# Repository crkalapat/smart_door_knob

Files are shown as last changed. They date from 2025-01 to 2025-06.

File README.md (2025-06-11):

# Smart Door Knob

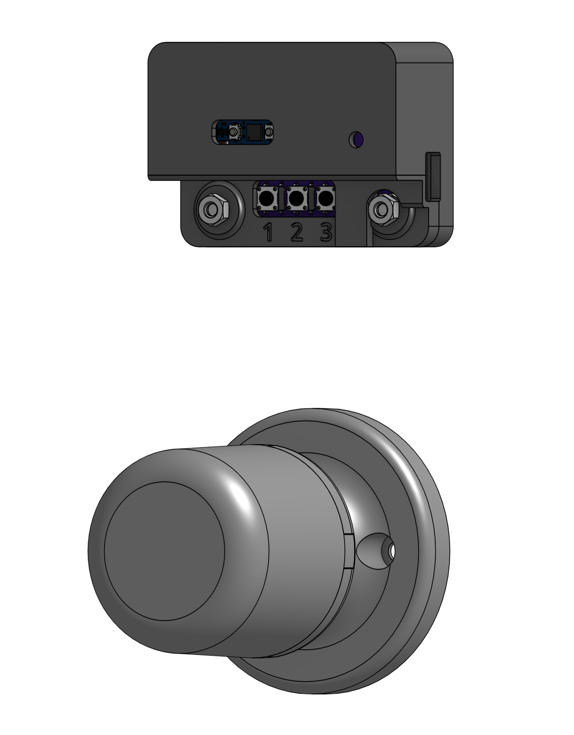
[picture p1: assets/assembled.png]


*A Matter compatible smart door knob*

## Overview
This smart door knob is designed specifically for Kwikset bed/room door knobs. The door knob is compatible with the [Matter](https://en.wikipedia.org/wiki/Matter_(standard)) smart home protocol, so it works with Amazon Alexa, Apple HomeKit, and Google Home. The only requirement is that you have a [Thread Border Router](https://www.matteralpha.com/explainer/thread-border-router) for the microcontroller (Arduino Nano Matter) to connect to.

## Instructions
After the code is flashed, you will need to set it up. You can use the QR Code link provided in the terminal, or use a manual pairing code. Once paired, (and whenever it turns on/resets after that) the RGB LED will begin to pulse blue. This signifies that it is in the process of connecting to the Thread Border Router that you specificed.

Once connected, the LED will turn off, indicating that the process has finished and that the door lock is ready to be controlled. You can then freely control the door lock either through your Matter smart home, or manually with the buttons. When the door is locked, the LED will be red, and when unlocked, the LED will be green. To unlock the door manually, enter the passcode specified in the code under the `buffer` variable (1-1-3-2 by default) using the corresponding buttons 1, 2, or 3. To lock the door manually, simply press any combination of incorrect buttons, and the door will lock if it wasn't locked already.

If you hit a wrong button and want to clear your input, simply wait for 5 seconds and all button input will be erased. If this is too long, the `inputWaitTime` variable can be customized in the code to change the clear time.

## Firmware Installation
Open the repo folder in Arduino IDE. If needed, pin numbers for components such as the RGB LED, servo, and buttons can be changed manually in the Arduino code file. Flash the code onto the Arduino Nano Matter. Once done, in the Serial Monitor (115200 baud), information for pairing the door lock can be found and used with a Matter compatible device.

## BOM
- 1x [Arduino Nano Matter with headers](https://store-usa.arduino.cc/collections/internet-of-things/products/nano-matter) (or [similar board](https://github.com/SiliconLabs/arduino/blob/main/readme.md))

- 2x 1x15 Socket Headers

- 1x [MG90 Servo](https://www.amazon.com/MG90S-Servo-Motor-Helicopter-Arduino/dp/B07L6FZVT1?crid=VYZSRM9027BT) (SG90 also works)

- 3x [6mm Push Buttons](https://www.amazon.com/DAOKI-Miniature-Momentary-Tactile-Quality/dp/B01CGMP9GY?crid=3P0EFZBRL88C4&)

- 1x [Micro USB Connector](https://www.mouser.com/ProductDetail/Amphenol-FCI/10118194-0011LF?qs=9lcNTSmDlCqQOdqcAswPOg%3D%3D)

- 1x [RGB LED](https://www.amazon.com/EDGELEC-Tri-Color-Multicolor-Diffused-Resistors/dp/B077XGF3YR?crid=3S7KMO6E8I0PC)

- 1x [PCB Board](pcb/)

- 8x M3x12mm screws

- 7x [Custom 3D-printed parts](cad/printed)

- 6x M3 nuts

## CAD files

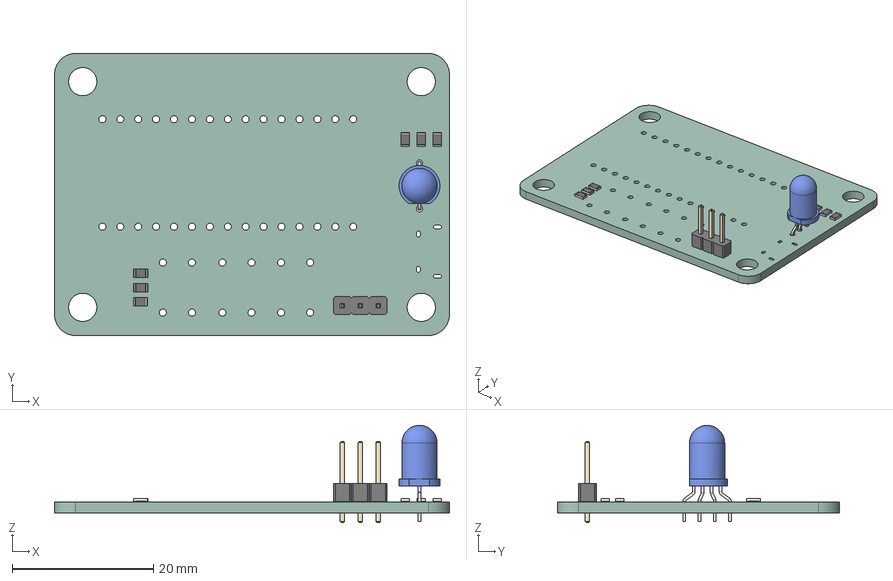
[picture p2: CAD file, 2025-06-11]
cad/pcb.step
56.0 x 40.0 x 13.8 mm
R_0805_2012Metric x 6
LED_D5.0mm-4_RGB_Wide_Pins
PinHeader_1x03_P254mm_Vertical
DoorKnob_PCB

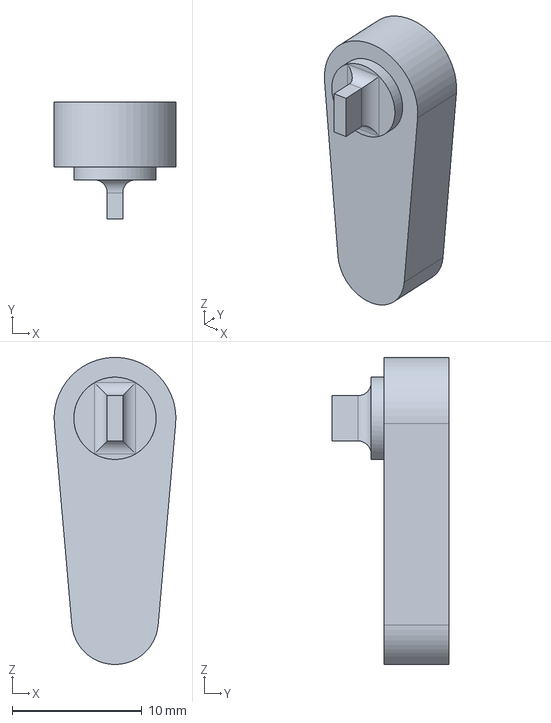
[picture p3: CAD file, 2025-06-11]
cad/printed/Servo Case.step
9.39 x 9.00 x 23.7 mm

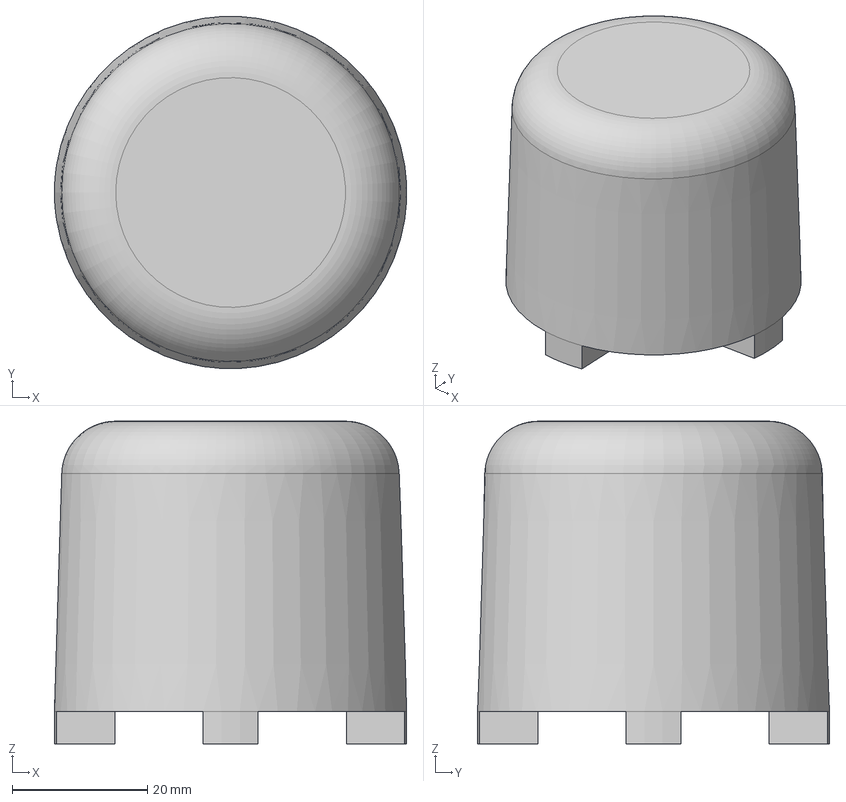
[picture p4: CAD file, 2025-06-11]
cad/printed/Knob Barrel.step
52.1 x 52.1 x 47.8 mm

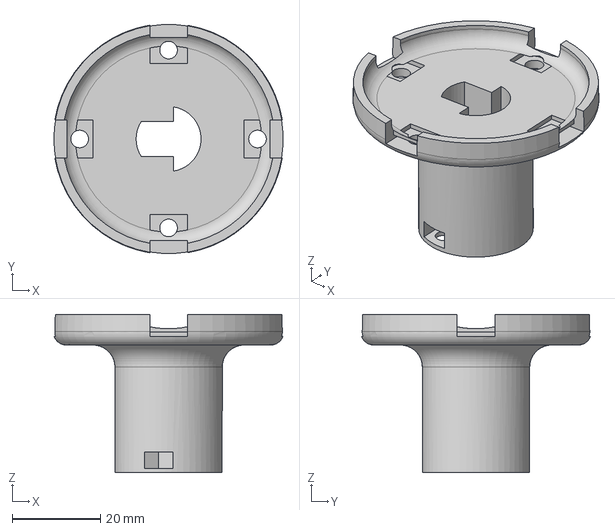
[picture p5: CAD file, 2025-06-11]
cad/printed/Knob Arm.step
52.0 x 52.0 x 36.0 mm

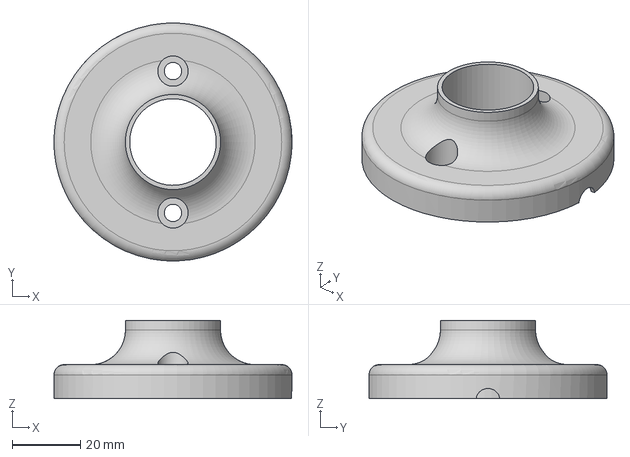
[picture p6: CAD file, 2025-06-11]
cad/printed/Knob Base.step
69.8 x 69.8 x 23.0 mm

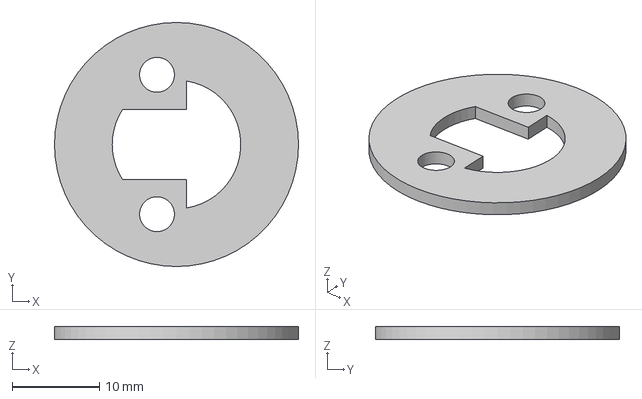
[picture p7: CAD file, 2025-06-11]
cad/printed/Knob Stopper.step
28.0 x 28.0 x 1.50 mm

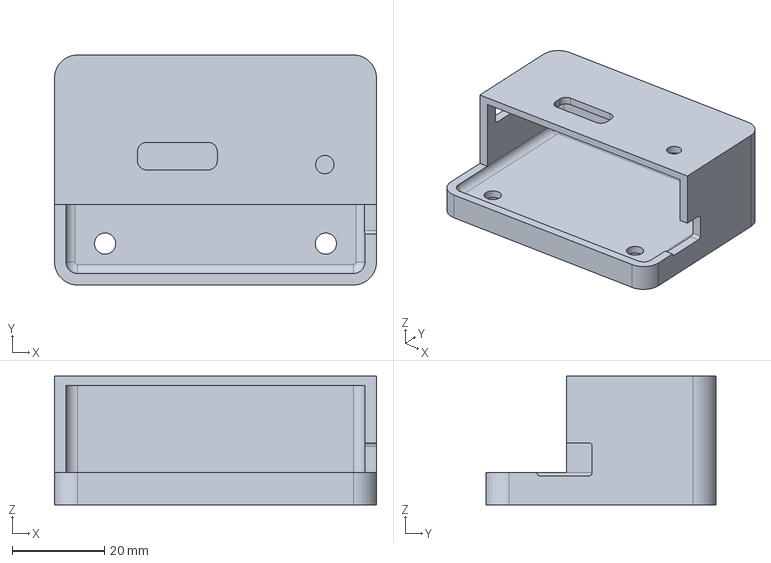
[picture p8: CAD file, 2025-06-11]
cad/printed/Electronics Enclosure.step
70.0 x 50.0 x 28.0 mm

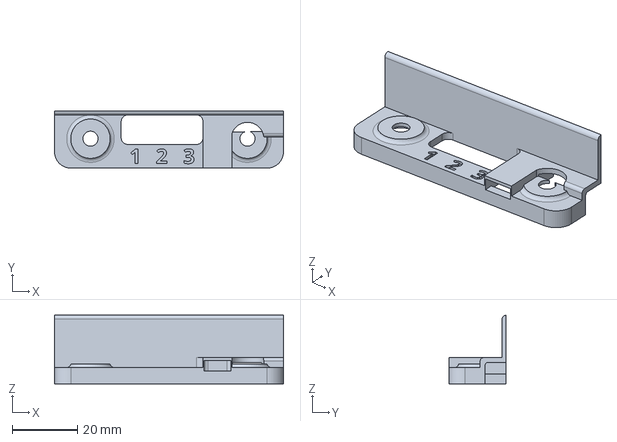
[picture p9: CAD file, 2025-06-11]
cad/printed/Electronics Lid.step
70.0 x 17.5 x 21.0 mm

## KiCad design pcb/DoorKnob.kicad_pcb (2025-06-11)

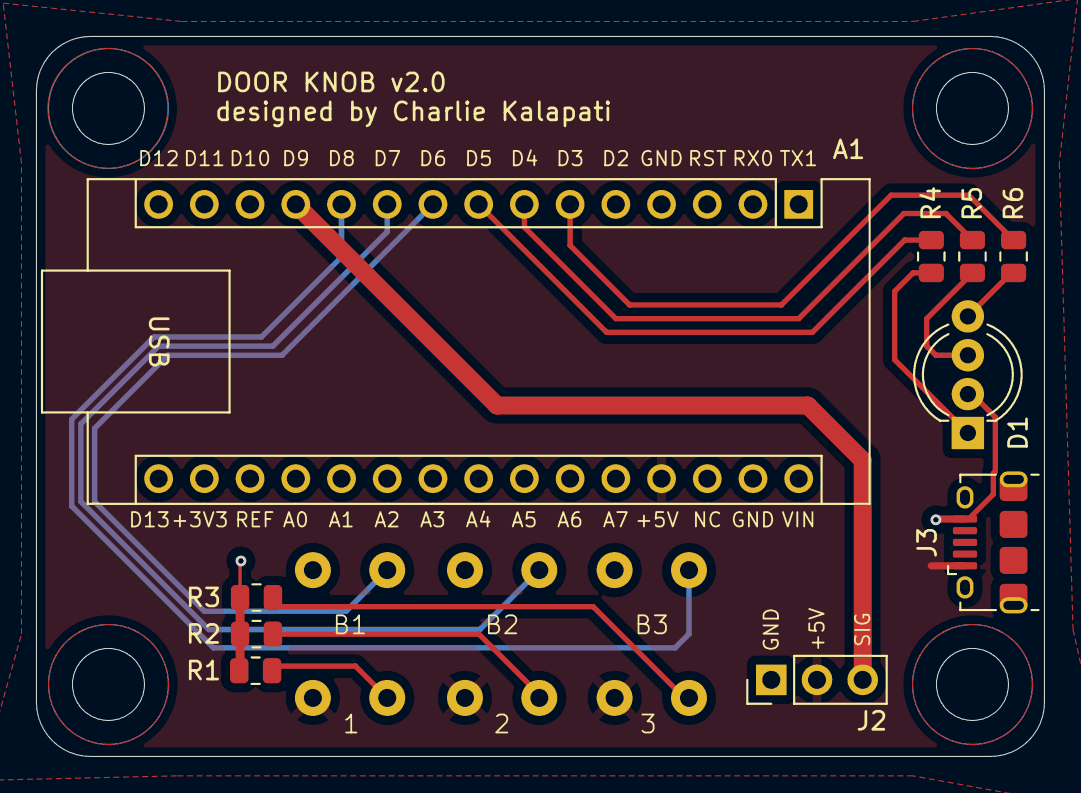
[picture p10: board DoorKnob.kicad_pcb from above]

Board: 2 copper layers, 56.0 x 40.0 mm, 13 parts (0 on the bottom side), 15 nets.

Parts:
A1: Arduino_Nano_Matter; Arduino_Nano
B1, B2, B3: Button_6mm
D1: LED_RKGB; LED_D5.0mm-4_RGB_Wide_Pins
J2: Conn_01x03; PinHeader_1x03_P2.54mm_Vertical
J3: USB_B_Micro; USB_Micro-B_Amphenol_10118194-0001LF_Horizontal
R1, R2, R3, R4, R5, R6: 220R; R_0805_2012Metric

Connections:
+5V: A1.27 (+5V), B1.3, B2.3, B3.3, J2.2, J3.1 (VBUS)
GND: A1.29 (GND), D1.2 (K), J2.1, J3.5 (GND), R1.2, R2.2, R3.2
unnamed: A1.6 (D3), R6.1
unnamed: A1.7 (D4), R5.1
unnamed: A1.8 (D5), R4.1
unnamed: A1.9 (D6), B1.2
unnamed: A1.10 (D7), B2.2
unnamed: A1.11 (D8), B3.2
unnamed: A1.12 (D9), J2.3
unnamed: B1.4, R1.1
unnamed: B2.4, R2.1
unnamed: B3.4, R3.1
unnamed: D1.4 (BA), R6.2
unnamed: D1.3 (GA), R5.2
unnamed: D1.1 (RA), R4.2

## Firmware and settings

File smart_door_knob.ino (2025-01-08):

/*
    Nano Matter Servo Lock
    by C. Kalapati

    A Matter door lock for the Arduino Nano Matter that rotates a servo via 
    PWM every time the lock is triggered to be unlocked or locked. 3 buttons 
    are used as input for a passcode for locking and unlocking.

    Derived from default Matter Door Lock code by Tamas Jozsi (Silicon Labs)
*/

#include <Matter.h>
#include <MatterDoorLock.h>
#include <vector>

#ifndef BTN_BUILTIN
#define BTN_BUILTIN PA0
#endif

/*-- Variables (to be modified to your use case) --*/

std::vector<int> passcode = {1, 1, 3, 2}; // Passcode to unlock door
const long inputWaitTime = 5000; // Time before clearing the buffer after last input (milliseconds)

const int servoPin = 9;
const int button1Pin = 6;
const int button2Pin = 7;
const int button3Pin = 8;
const int ledRedPin = 5;
const int ledGreenPin = 4;
const int ledBluePin = 3;

/*-------------------------------------------------*/

const int minPulseWidth = 500; // Min pulse width in microseconds
const int maxPulseWidth = 2500; // Max pulse width in microseconds
const int servoMinAngle = 0;
const int servoMaxAngle = 180;

volatile bool button_pressed = false;
volatile bool button1_pressed = false;
volatile bool button2_pressed = false;
volatile bool button3_pressed = false;

unsigned long previousMicros = 0; // Store time in microseconds
unsigned long pulseDuration = 0;
unsigned long period = 20000;    // Total PWM period in microseconds (20 ms)
int servoState = LOW;

unsigned long previousMillis = 0; // Store time in milliseconds
int previousBufferSize = 0;

MatterDoorLock matter_door_lock;
std::vector<int> buffer;

void set_servo_angle(int);
void handle_button_press();
void handle_passcode_input(int);
void handle_button_press3();
void handle_button_press2();
void handle_button_press1();

void setup()
{
  Serial.begin(115200);
  Matter.begin();
  matter_door_lock.begin();

  pinMode(servoPin, OUTPUT);
  pinMode(ledRedPin, OUTPUT);
  pinMode(ledBluePin, OUTPUT);
  pinMode(ledGreenPin, OUTPUT);

  pinMode(button1Pin, INPUT_PULLUP);
  pinMode(button2Pin, INPUT_PULLUP);
  pinMode(button3Pin, INPUT_PULLUP);

  pinMode(BTN_BUILTIN, INPUT_PULLUP);
  attachInterrupt(BTN_BUILTIN, &handle_button_press, FALLING);
  attachInterrupt(button1Pin, &handle_button_press1, FALLING);
  attachInterrupt(button2Pin, &handle_button_press2, FALLING);
  attachInterrupt(button3Pin, &handle_button_press3, FALLING);

  pinMode(LED_BUILTIN, OUTPUT);
  digitalWrite(LED_BUILTIN, LED_BUILTIN_INACTIVE);

  Serial.println("Matter door lock");

  // Pairing information for the door lock with Matter devices
  if (!Matter.isDeviceCommissioned()) {
    Serial.println("Matter device is not commissioned");
    Serial.println("Commission it to your Matter hub with the manual pairing code or QR code");
    Serial.printf("Manual pairing code: %s\n", Matter.getManualPairingCode().c_str());
    Serial.printf("QR code URL: %s\n", Matter.getOnboardingQRCodeUrl().c_str());
  }

  Serial.printf("Manual pairing code: %s\n", Matter.getManualPairingCode().c_str());
  Serial.printf("QR code URL: %s\n", Matter.getOnboardingQRCodeUrl().c_str());

  // Connect to the Matter and Thread network before starting
  while (!Matter.isDeviceCommissioned()) {
    delay(200);
  }

  Serial.println("Waiting for Thread network...");
  while (!Matter.isDeviceThreadConnected()) {
    delay(200);
  }
  Serial.println("Connected to Thread network");

  Serial.println("Waiting for Matter device discovery...");
  while (!matter_door_lock.is_online()) {

    // Cycle through a loading animation with the Blue LED
    for (int i = 0; i < 100; i++) {
      analogWrite(ledBluePin, i);
      delay(5);
    }
    for (int i = 100; i >= 0; i--) {
      analogWrite(ledBluePin, i);
      delay(5);
    }
    delay(100);
  }
  Serial.println("Matter device is now online");
}

void loop()
{

  bool locked = matter_door_lock.is_locked();

  if (buffer.size() == 4) {
    if (buffer == passcode) {
      matter_door_lock.toggle();
    } else {

      // Lock the door if it is unlocked after incorrect input
      if (!locked) {
        matter_door_lock.toggle();
      }
    }
    buffer.clear();
  } else if (buffer.size() != 0) {

    unsigned long currentMillis = millis();

    // Check to see if the inputWaitTime time has elapsed
    if (currentMillis - previousMillis > inputWaitTime) {
      buffer.clear();
    }
  }

  static bool locked_last = false;

  if (locked != locked_last) {
    locked_last = locked;
    if (locked) {
      Serial.println("Locked");
      analogWrite(ledRedPin, 100);
      analogWrite(ledGreenPin, 0);
      digitalWrite(ledBluePin, LOW);
      set_servo_angle(0);
    } else {
      Serial.println("Unlocked");
      analogWrite(ledRedPin, 0);
      analogWrite(ledGreenPin, 50);
      digitalWrite(ledBluePin, LOW);
      set_servo_angle(80);
    }
  }


  // lock door if built in button is pressed
  if (button_pressed) {
    button_pressed = false;
    matter_door_lock.toggle();
  }
}

void handle_button_press()
{

  static uint32_t btn_last_press = 0;
  if (millis() < btn_last_press + 200) {
    return;
  }
  btn_last_press = millis();
  button_pressed = true;
  
}

void handle_button_press1()
{
  Serial.println("Button 1 Pressed");
  static uint32_t btn_last_press = 0;
  if (millis() < btn_last_press + 200) {
    return;
  }
  btn_last_press = millis();
  handle_passcode_input(1);
}

void handle_button_press2()
{
  Serial.println("Button 2 Pressed");
  static uint32_t btn_last_press = 0;
  if (millis() < btn_last_press + 200) {
    return;
  }
  btn_last_press = millis();
  handle_passcode_input(2);
}

void handle_button_press3()
{
  Serial.println("Button 3 Pressed");
  static uint32_t btn_last_press = 0;
  if (millis() < btn_last_press + 200) {
    return;
  }
  btn_last_press = millis();
  handle_passcode_input(3);
}

void set_servo_angle(int angle) {

  if (angle < servoMinAngle) {
    angle = servoMinAngle;
  }

  int pulseWidth = map(angle, servoMinAngle, 180, minPulseWidth, maxPulseWidth);

  for (int i = 0; i < 20; i++) {
    digitalWrite(servoPin, HIGH);
    delayMicroseconds(pulseWidth);
    digitalWrite(servoPin, LOW);
    delayMicroseconds(20000 - pulseWidth);
  }
}

void handle_passcode_input(int number) {

  previousMillis = millis();
  buffer.push_back(number);

}

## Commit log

2025-06-11 Update README, add images and CAD
    [Electronics Enclosure.step, Electronics Lid.step, Knob Arm.step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]
2025-06-11 Add PCB files
    [DoorKnob.kicad_pcb, DoorKnob.kicad_sch, pcb.step]
